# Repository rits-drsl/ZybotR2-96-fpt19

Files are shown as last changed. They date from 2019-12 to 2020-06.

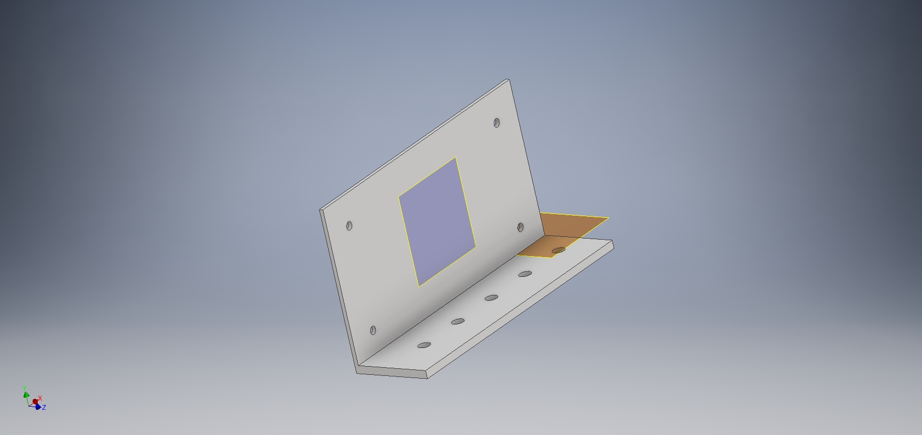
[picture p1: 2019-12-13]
assets/cad/avhzy_mounter/avhzy_mounter.jpg

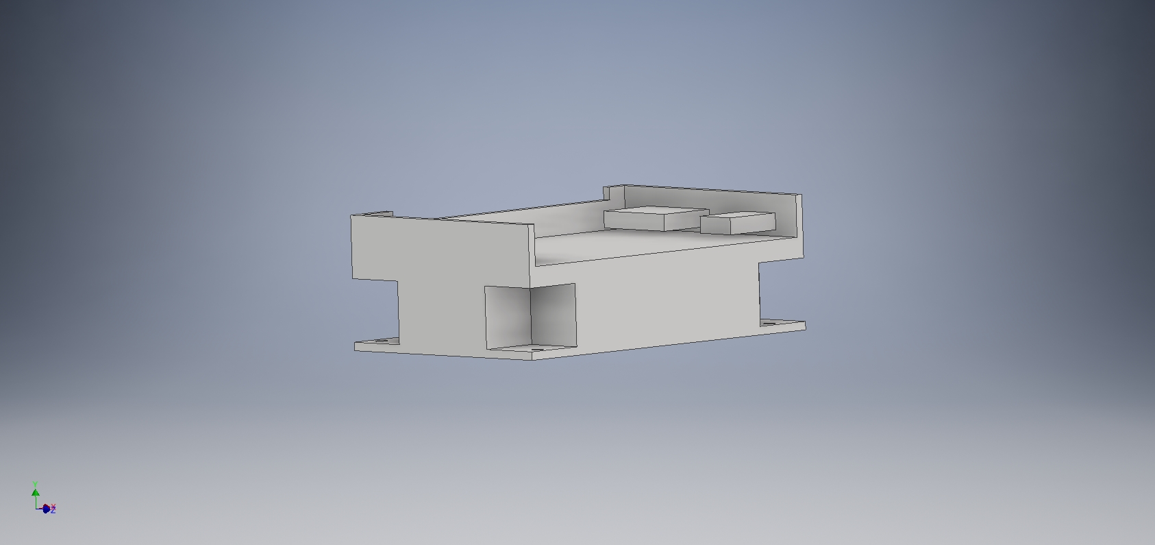
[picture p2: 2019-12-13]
assets/cad/ultra96_holder/ultra96_holder.jpg

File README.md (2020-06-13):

# ZybotR2-96-fpt19
An UGV-system using SoC-FPGA developed for FPGA design competition held on ICFPT2019.

**Our team won first place! :tada: :tada: :tada:**
<p align="center">
    ZybotR2-96
</p>

## Features
- **Localization** and **Motion Planning** are implemented in the UGV-system
    - In the **Localization** process, observations such as **Wheel Odometry** are fusioned by **Particle Filter**
    - In the **Motion Planning** process, **Informed-RRT\***, **Pure Pursuit**, and **PID control** are used
debug

- Efficient data flow that image data captured by image sensor are processed by FPGA before transferring to DRAM
- Peripheral devices (e.g. DC motor) can be handled transparently from Zynq PS by a system that synchronize registers between multiple FPGAs with UART
<p align="center">
    architecture
</p>

- The UGV-system is divided into **five layers**, and it is descending order of abstraction
<p align="center">
    system_layer
</p>

## Main Parts of The Vehicle
- [Avnet Ultra96 V1](https://www.xilinx.com/products/boards-and-kits/1-vad4rl.html)
- [Digilent Cmod A7-35T](https://reference.digilentinc.com/reference/programmable-logic/cmod-a7/start/)
- [96Boards MIPI Adapter Mezzanine](https://www.96boards.org/product/mipiadapter/)
- [Pcam5C](https://store.digilentinc.com/pcam-5c-5-mp-fixed-focus-color-camera-module/)
- [Web Camera (Buffalo BSW20KM11BK)](https://www.buffalo.jp/product/detail/bsw20km11bk.html)
- [Stereo Camera (Optor)](https://www.seeedstudio.com/Optor-Cam2pc-Visual-Inertial-SLAM-p-307.html)
- [Anker PowerCore+ 26800 PD](https://www.anker.com/products/variant/powercore--26800-pd-with-30w-power-delivery-charger/B1375112)
- [DC Motor/Gearbox (1:53 Gear Ratio)](https://store.digilentinc.com/dc-motor-gearbox-1-53-gear-ratio-custom-6v-motor-designed-for-digilent-robot-kits/)

## Repository Structure
A part of this repository structure is shown below:

``` sh
ZybotR2-96-fpt19
├── assets
│   ├── cad
│   ├── script
│   └── tools
├── cmod-a7
│   └── vivado
│       ├── prj
│       └── src
└── ultra96
    ├── BOOT_FS
    ├── ROOT_FS
    │   ├── app
    │   │   ├── fad
    │   │   └── other
    │   ├── driver
    │   │   ├── cp210x
    │   │   ├── usbserial
    │   │   └── v4l2
    │   ├── dts
    │   ├── firmware
    │   ├── lib
    │   │   ├── control
    │   │   ├── improc
    │   │   ├── optor
    │   │   ├── planner
    │   │   └── zynqpl
    │   └── package
    └── vivado
        ├── ip
        ├── prj
        └── src
```

- `assets/`
    - 3DCAD data for the vehicle parts, scripts which install libraries such as OpenCV, and tools are stored
- `cmod/vivado/`
    - RTL files and scripts which create project are stored
    - A Registers synchronization module, a motor controller, and an OLED controller are implemented
- `ultra96/BOOT_FS/`
    - Binary files for booting Linux on Ultra96 are stored
    - These files are prepared with reference to [ikwzm/ZynqMP-FPGA-Linux](https://github.com/ikwzm/ZynqMP-FPGA-Linux)
- `ultra96/ROOT_FS/app/`
    - An application of FAD(FPGA Autonomous Driving), test applications of devices, and so on are stored
- `ultra96/ROOT_FS/lib/`
    - Shared libraries are stored
    - `planner` is based on [kyk0910/sampling-based-planners](https://github.com/kyk0910/sampling-based-planners)
    - `optor` is prepared with reference to [optor-vis/optor_vi-stereo-v1](https://github.com/optor-vis/optor_vi-stereo-v1)
- `ultra96/ROOT_FS/driver/`
    - Device drivers are stored
    - `v4l2` which is Linux V4L2 driver which deals with the Xilinx VDMA IP is prepared with reference to [fixstars/ultra96_design](https://github.com/fixstars/ultra96_design)
- `ultra96/ROOT_FS/dts/`
    - DTS(Device Tree Source) files are stored
    - We reflect some of device information to kernel using **Device Tree Overlay** which is feature of Linux kernel
- `ultra96/ROOT_FS/firmware/`
    - A bitstream file and firmware of wireless LAN modules are stored
    - A bitstream file is loaded with **FPGA Region** which is feature of Linux kernel
- `ultra96/ROOT_FS/package/`
    - Debian packages of **linux-headers** and **linux-image** are stored
    - There are also prepared with reference to [ikwzm/ZynqMP-FPGA-Linux](https://github.com/ikwzm/ZynqMP-FPGA-Linux)
- `ultra96/vivado/`
    - RTL files, HLS sources, IPs made by Digilent and scripts which create project are stored
    - `preimproc` module is based on [kyk0910/HLS-canny-edge-detection](https://github.com/kyk0910/HLS-canny-edge-detection)

## Future Work
- Offload computation heavy processes such as Informed-RRT*, Particle Filter, path tracking algorithms, and calculating Visual Odometry
- Implement more accurate image recognition algorithms

## Links
- [2019 International Conference on Field-Programmable Technology FPGA Design Competition](http://fpt19.tju.edu.cn/Contest/FPT2019_FPGA_Design_Competition.htm)

## Authors
- [Yuya Kudo](https://github.com/medalotte)
- [Atsushi Takada](https://github.com/atlchemt)
- [Yuta Ishida](https://github.com/yukkuriDo)
- Prof. Tomonori Izumi

## References
[Y. Kudo, A. Takada, Y. Ishida, and T. Izumi, "An SoC-FPGA-based Micro UGV with Localization and Motion Planning," in Proceedings of 2019 International Conference on Field-Programmable Technology (ICFPT), 2019, pp. 469-472.](https://ieeexplore.ieee.org/document/8977887)

## License
MIT

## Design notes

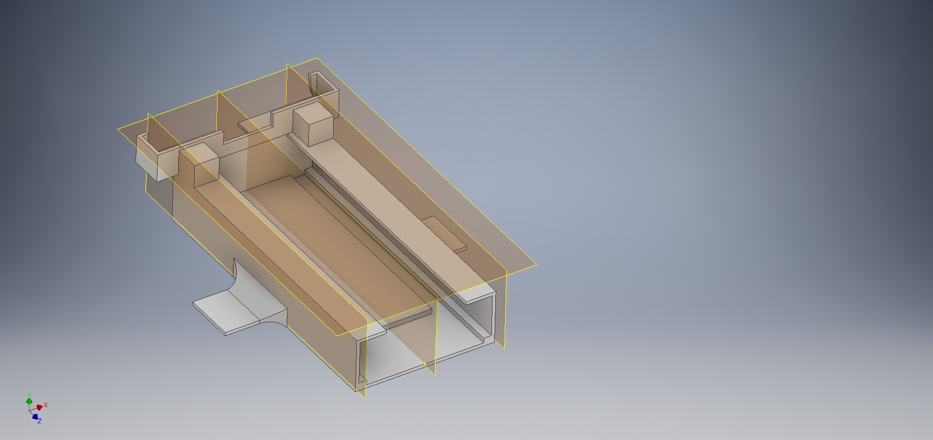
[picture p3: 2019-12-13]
assets/cad/battery_case/battery_case.jpg

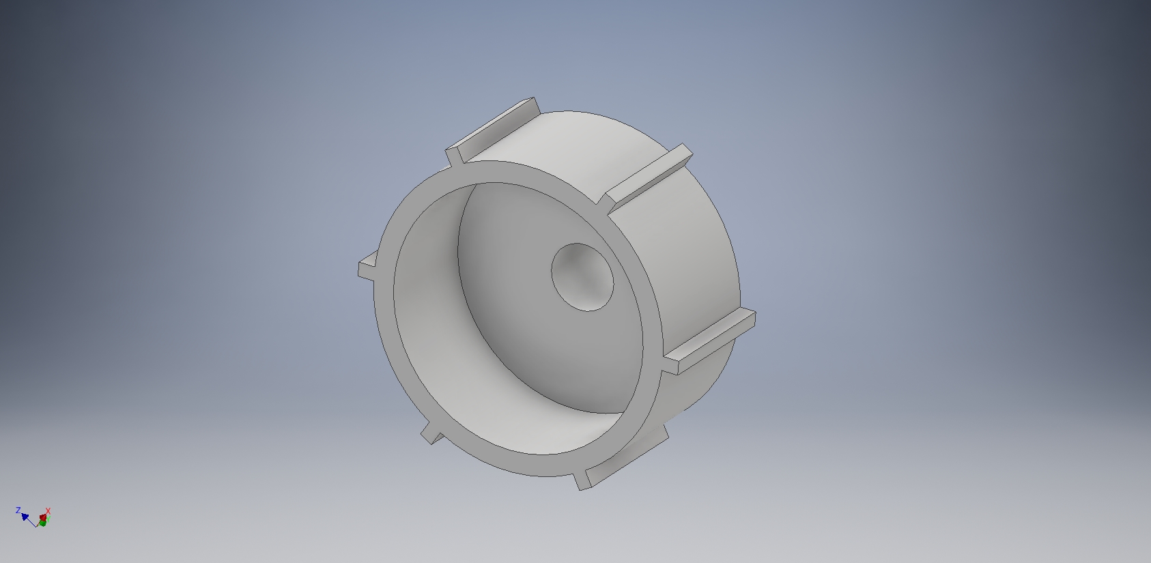
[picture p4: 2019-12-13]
assets/cad/camera_cap_holder/camera_cap_holder.jpg

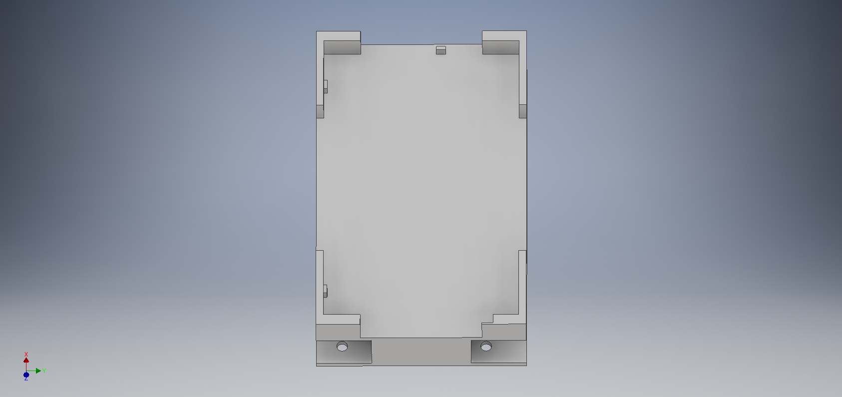
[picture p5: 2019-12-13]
assets/cad/cmod_a7_holder/cmod_a7_holder.jpg

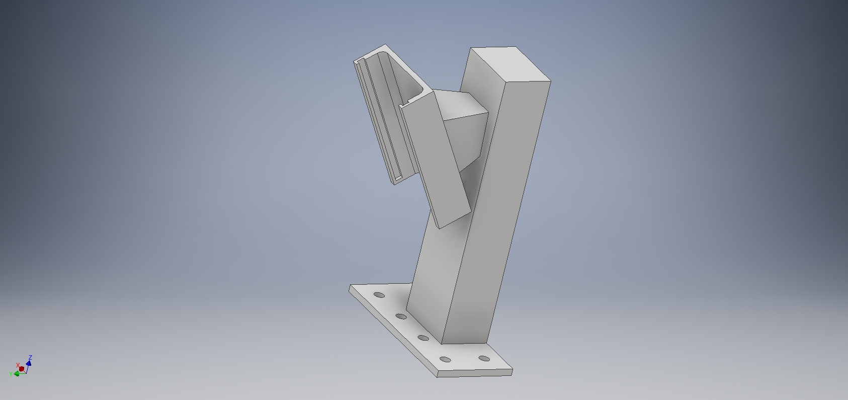
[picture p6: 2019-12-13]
assets/cad/Pcam5C/Pcam5C_mounter.jpg

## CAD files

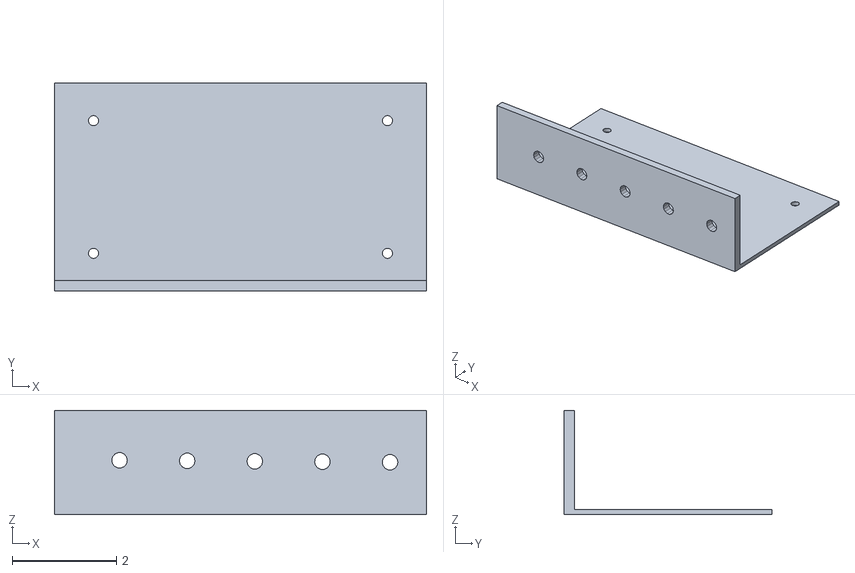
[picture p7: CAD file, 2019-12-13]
assets/cad/avhzy_mounter/avhzy_mounter.stl
7.15 x 4.00 x 2.00

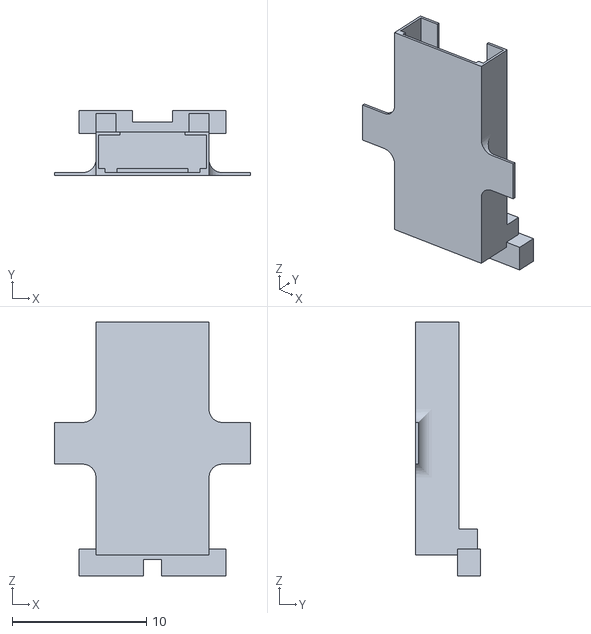
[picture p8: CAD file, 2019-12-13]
assets/cad/battery_case/battery_case.stl
14.6 x 4.82 x 19.0

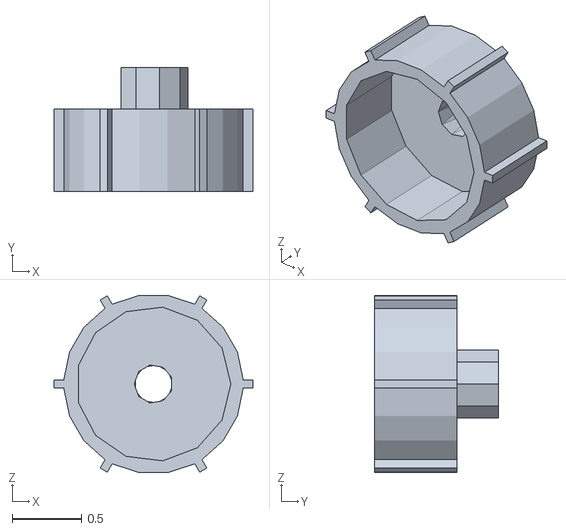
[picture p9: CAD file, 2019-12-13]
assets/cad/camera_cap_holder/camera_cap_holder.stl
1.44 x 0.9 x 1.28

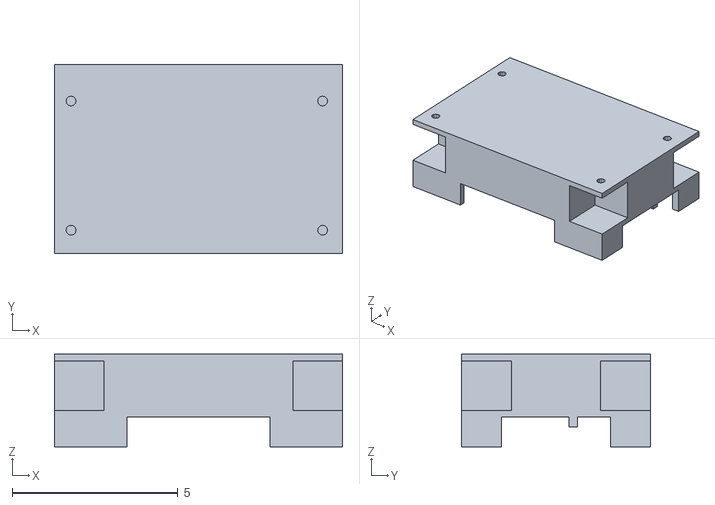
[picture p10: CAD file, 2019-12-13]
assets/cad/cmod_a7_holder/cmod_a7_holder.stl
8.70 x 5.70 x 2.80

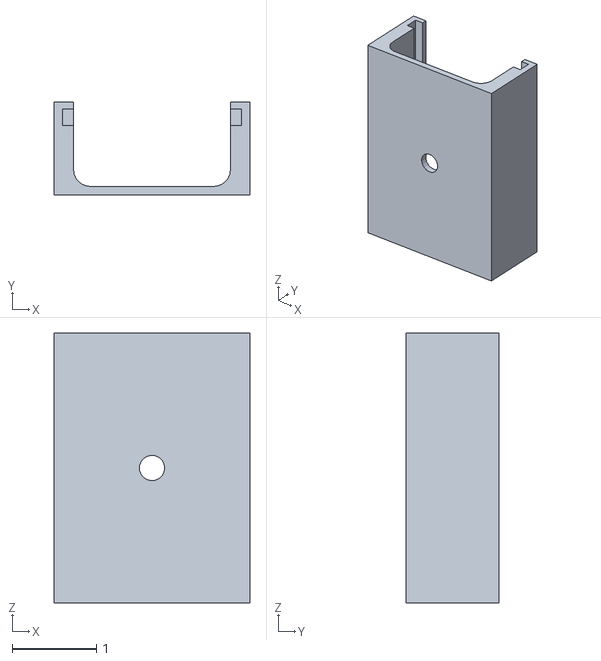
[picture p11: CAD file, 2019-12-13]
assets/cad/HB5_holder/HB5_holder.stl
2.32 x 1.10 x 3.20

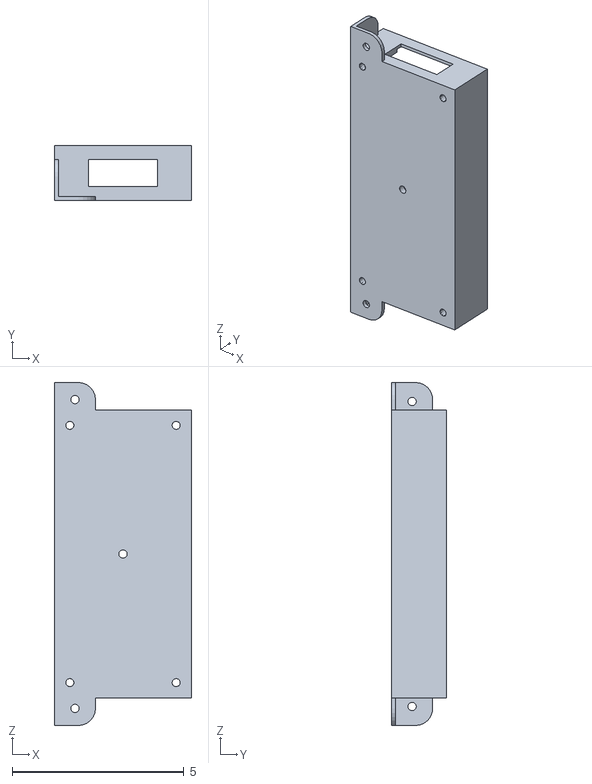
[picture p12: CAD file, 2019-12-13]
assets/cad/OLED_holder/OLED_holder.stl
4.00 x 1.60 x 10.0

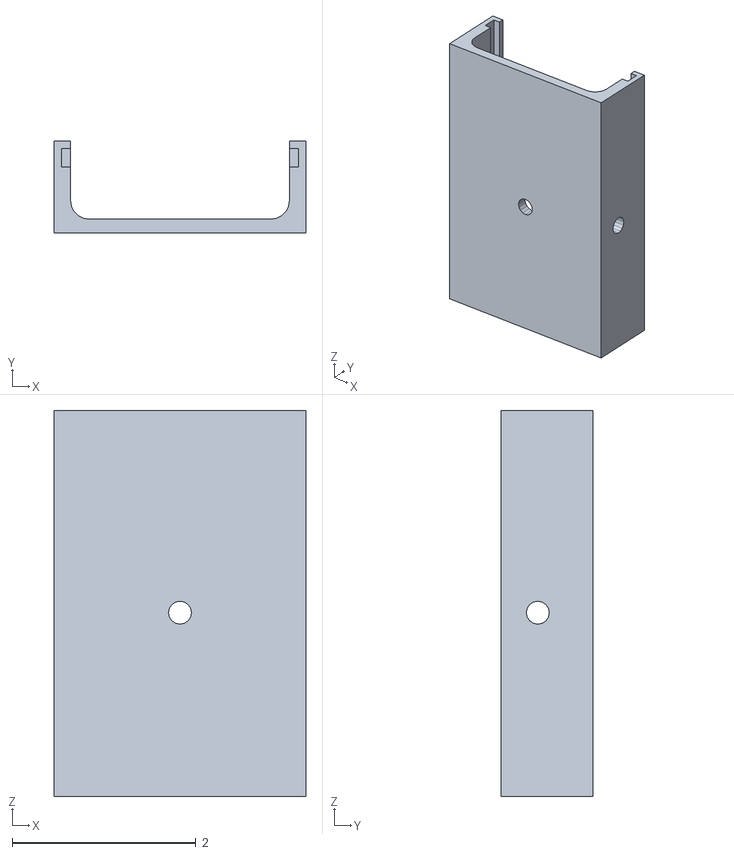
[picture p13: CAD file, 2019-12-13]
assets/cad/Pcam5C/Pcam5C_holder.stl
2.74 x 1.00 x 4.20

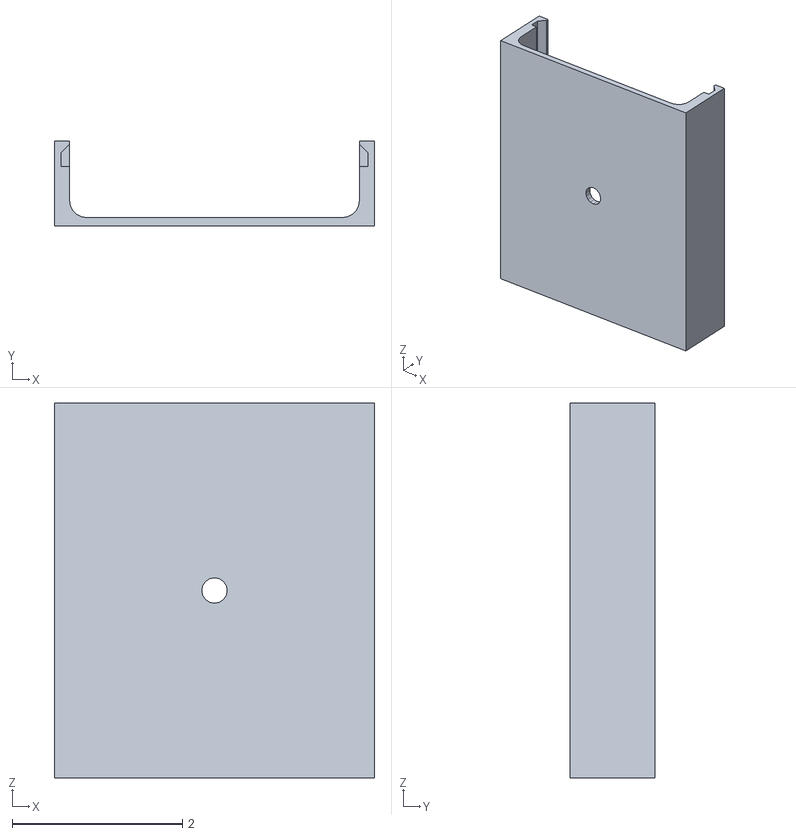
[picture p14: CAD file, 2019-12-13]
assets/cad/protection_circuit_holder/protection_circuit_holder.stl
3.76 x 1.00 x 4.40

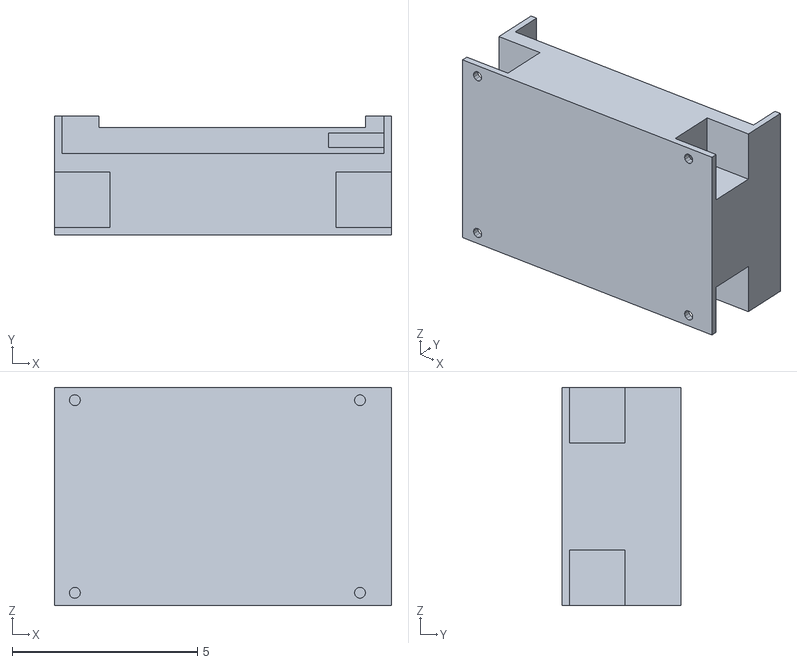
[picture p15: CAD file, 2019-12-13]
assets/cad/ultra96_holder/ultra96_holder.stl
9.10 x 3.20 x 5.90

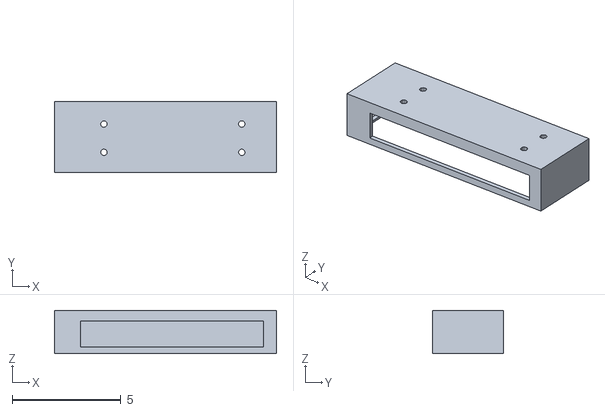
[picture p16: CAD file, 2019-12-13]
assets/cad/usb_hub_holder/usb_hub_holder.stl
10.2 x 3.25 x 2.00

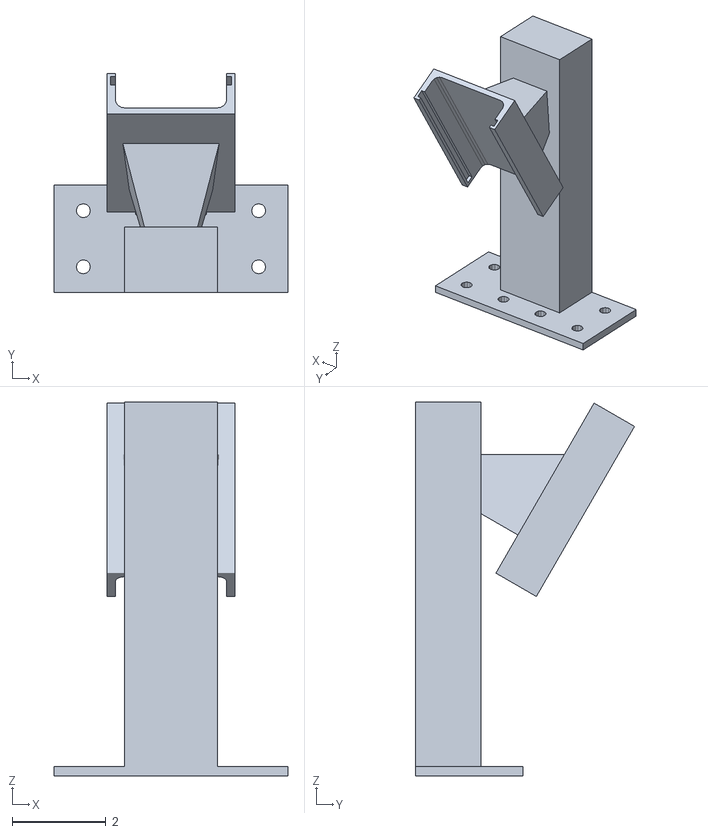
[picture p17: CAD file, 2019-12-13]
assets/cad/Pcam5C/Pcam5C_mounter.stl
5.00 x 4.69 x 8.00

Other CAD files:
assets/cad/HB5_holder/HB5_holder.ipt
assets/cad/OLED_holder/OLED_holder.ipt
assets/cad/Pcam5C/Pcam5C_holder.ipt
assets/cad/Pcam5C/Pcam5C_mounter.ipt
assets/cad/avhzy_mounter/avhzy_mounter.ipt
assets/cad/battery_case/battery_case.ipt
assets/cad/camera_cap_holder/camera_cap_holder.ipt
assets/cad/cmod_a7_holder/cmod_a7_holder.ipt
assets/cad/protection_circuit_holder/protection_circuit_holder.ipt
assets/cad/ultra96_holder/ultra96_holder.ipt
assets/cad/usb_hub_holder/usb_hub_holder.ipt

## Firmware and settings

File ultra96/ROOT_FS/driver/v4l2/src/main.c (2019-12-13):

#include <linux/kernel.h>
#include <linux/module.h>
#include <linux/types.h>
#include <linux/of_platform.h>
#include <linux/dma-mapping.h>
#include <linux/interrupt.h>
#include <linux/poll.h>
#include <linux/videodev2.h>
#include "zynq_v4l2.h"

MODULE_DESCRIPTION("ZYNQ v4l2 device driver");
MODULE_AUTHOR("takashi.osawa");
MODULE_LICENSE("GPL");

int vdma_h_res = 1280;
int vdma_v_res = 720;
module_param(vdma_h_res, int, S_IRUGO);
module_param(vdma_v_res, int, S_IRUGO);
MODULE_PARM_DESC(vdma_h_res, "v4l2 buffer width");
MODULE_PARM_DESC(vdma_v_res, "v4l2 buffer height");

int zynq_v4l2_find_oldest_slot(uint32_t slot_bits, int latest)
{
    uint32_t bits = slot_bits;

    bits &= ~(((1 << latest) << 1) - 1);
    if (bits ) {
        return __builtin_ctz(bits);
    } else if (slot_bits) {
        return __builtin_ctz(slot_bits);
    } else {
        return -1;
    }
}

static int zynq_v4l2_open(struct inode *inode, struct file *filp)
{
    struct zynq_v4l2_sys_data *sp;
    struct zynq_v4l2_dev_data *dp;
    int minor;

    PRINTK(KERN_INFO "%s\n", __FUNCTION__);

    sp = container_of(inode->i_cdev, struct zynq_v4l2_sys_data, cdev);
    if (sp == NULL) {
        printk(KERN_ERR "container_of failed\n");
        return -EFAULT;
    }
    minor = iminor(inode);
    dp = &sp->dev[minor];
    filp->private_data = dp;

    return 0;
}

static int zynq_v4l2_close(struct inode *inode, struct file *filp)
{
    struct zynq_v4l2_dev_data *dp = filp->private_data;

    PRINTK(KERN_INFO "%s\n", __FUNCTION__);

    zynq_v4l2_vdma_intr_disable(dp);
    spin_lock_irq(&dp->lock);
    dp->ctrl.queue_bits = 0;
    dp->ctrl.active_bits = 0;
    spin_unlock_irq(&dp->lock);
    while (dp->ctrl.work_queue_active) {
        schedule();
    }
    if (dp->mem.mmap) {
        #ifdef USE_VMALLOC
        vfree(dp->mem.mmap);
        #else /* !USE_VMALLOC */
        dma_free_coherent(dp->dma_dev, ALIGN(dp->frame.size, PAGE_SIZE) * dp->frame.user_count, dp->mem.mmap, dp->mem.phys_mmap);
        #endif /* !USE_VMALLOC */
        dp->mem.mmap = NULL;
    }

    return 0;
}

static ssize_t zynq_v4l2_read(struct file *filp, char __user *buf, size_t count, loff_t *f_pos)
{
    struct zynq_v4l2_dev_data *dp = filp->private_data;
    int wb;

    if (count > vdma_h_res * vdma_v_res * 3) {
        return -EINVAL;
    }

    wb = XAxiVdma_CurrFrameStore(dp->vdma.inst, XAXIVDMA_WRITE);
    wb = (wb + dp->vdma.inst->MaxNumFrames - 1) % dp->vdma.inst->MaxNumFrames;
    printk(KERN_INFO "%s wb = %d\n", __FUNCTION__, wb);
    if (raw_copy_to_user(buf, dp->vdma.virt_wb + dp->frame.size * wb, count) != 0) {
        return -EFAULT;
    }

    return count;
}

static ssize_t zynq_v4l2_write(struct file *filp, const char __user *buf, size_t count, loff_t *f_pos)
{
    PRINTK(KERN_INFO "%s\n", __FUNCTION__);

    return 0;
}

static unsigned int zynq_v4l2_poll(struct file *filp, struct poll_table_struct *waitp)
{
    struct zynq_v4l2_dev_data *dp = filp->private_data;
    int slot, rc;

    PRINTK(KERN_INFO "%s\n", __FUNCTION__);

    spin_lock_irq(&dp->lock);
    slot = zynq_v4l2_find_oldest_slot(dp->ctrl.active_bits, dp->ctrl.latest_frame);
    spin_unlock_irq(&dp->lock);

    if (slot == -1) {
        poll_wait(filp, &dp->ctrl.waitq, waitp);
        spin_lock_irq(&dp->lock);
        if ((slot = zynq_v4l2_find_oldest_slot(dp->ctrl.active_bits, dp->ctrl.latest_frame)) == -1) {
            rc = 0;
        } else {
            rc = (POLLIN | POLLRDNORM);
        }
        spin_unlock_irq(&dp->lock);
    } else {
        rc = (POLLIN | POLLRDNORM);
    }
    PRINTK(KERN_INFO "  rc = %d, slot = %d\n", rc, slot);

    return rc;
}

static int zynq_v4l2_vma_fault(struct vm_fault *vmf)
{
    struct page *page;
    unsigned long offset = vmf->pgoff << PAGE_SHIFT;
    struct zynq_v4l2_dev_data *dp = vmf->vma->vm_private_data;

    if (offset > dp->frame.size * dp->frame.user_count) {
        return VM_FAULT_SIGBUS;
    }

    #ifdef USE_VMALLOC
    page = vmalloc_to_page((void *)((unsigned long)dp->mem.mmap + offset));
    #else /* !USE_VMALLOC */
    page = phys_to_page(dp->mem.phys_mmap + offset);
    #endif /* !USE_VMALLOC */
    get_page(page);
    vmf->page = page;

    return 0;
}

static struct vm_operations_struct zynq_v4l2_vm_ops = {
                                                       .fault = zynq_v4l2_vma_fault,
};

static int zynq_v4l2_mmap(struct file *filp, struct vm_area_struct *vma)
{
    struct zynq_v4l2_dev_data *dp = filp->private_data;

    PRINTK(KERN_INFO "%s\n", __FUNCTION__);

    if ((vma->vm_pgoff + vma_pages(vma)) > ((ALIGN(dp->frame.size, PAGE_SIZE) * dp->frame.user_count) >> PAGE_SHIFT)) {
        return -EINVAL;
    }

    vma->vm_private_data = dp;
    vma->vm_ops = &zynq_v4l2_vm_ops;

    return 0;
}

static struct file_operations zynq_v4l2_fops = {
                                                .open           = zynq_v4l2_open,
                                                .release        = zynq_v4l2_close,
                                                .read           = zynq_v4l2_read,
                                                .write          = zynq_v4l2_write,
                                                .poll           = zynq_v4l2_poll,
                                                .unlocked_ioctl = zynq_v4l2_ioctl,
                                                .compat_ioctl   = zynq_v4l2_ioctl,
                                                .mmap           = zynq_v4l2_mmap,
};

static int zynq_v4l2_create_cdev(struct device *parent, struct zynq_v4l2_sys_data *sp)
{
    int ret;
    dev_t dev;
    int minor;

    PRINTK(KERN_INFO "%s\n", __FUNCTION__);

    ret = alloc_chrdev_region(&dev, MINOR_BASE, MINOR_NUM, DRIVER_NAME);
    if (ret != 0) {
        printk(KERN_ERR "alloc_chrdev_region = %d\n", ret);
        return -1;
    }

    sp->class = class_create(THIS_MODULE, DRIVER_NAME);
    if (IS_ERR(sp->class)) {
        printk(KERN_ERR "class_create\n");
        goto error;
    }

    cdev_init(&sp->cdev, &zynq_v4l2_fops);
    sp->cdev.owner = THIS_MODULE;
    sp->major = MAJOR(dev);

    ret = cdev_add(&sp->cdev, dev, MINOR_NUM);
    if (ret != 0) {
        printk(KERN_ERR "cdev_add = %d\n", ret);
        goto error;
    }
    sp->cdev_inited = true;

    for (minor = 0; minor < MINOR_NUM; minor++) {
        struct zynq_v4l2_dev_data *dp = &sp->dev[minor];

        device_create(sp->class, parent, MKDEV(sp->major, minor), dp, "pcam%d", minor);
        dp->dma_dev = parent;
    }

    return 0;

 error:
    for (minor = 0; minor < MINOR_NUM; minor++) {
        if (sp->class) {
            device_destroy(sp->class, MKDEV(sp->major, minor));
        }
    }
    if (sp->cdev_inited) {
        cdev_del(&sp->cdev);
        sp->cdev_inited = false;
    }
    if (sp->class) {
        class_destroy(sp->class);
        sp->class = NULL;
    }
    unregister_chrdev_region(dev, MINOR_NUM);

    return -1;
}

static void zynq_v4l2_delete_cdev(struct zynq_v4l2_sys_data *sp)
{
    int minor;
    dev_t dev = MKDEV(sp->major, MINOR_BASE);

    PRINTK(KERN_INFO "%s\n", __FUNCTION__);

    for (minor = MINOR_BASE; minor < MINOR_BASE + MINOR_NUM; minor++) {
        device_destroy(sp->class, MKDEV(sp->major, minor));
    }
    if (sp->cdev_inited) {
        cdev_del(&sp->cdev);
    }
    class_destroy(sp->class);
    unregister_chrdev_region(dev, MINOR_NUM);
}

static int zynq_v4l2_hw_init(struct device *dev, struct zynq_v4l2_sys_data *sp)
{
    int minor, rc;

    PRINTK(KERN_INFO "%s\n", __FUNCTION__);

    if (zynq_v4l2_vdma_init(dev, sp)) {
        return -ENODEV;
    }

    /* if (zynq_v4l2_demosaic_init()) { */
    /*      rc = -ENODEV; */
    /*      goto error; */
    /* } */

    if (zynq_v4l2_mipicsi_init()) {
        rc = -ENODEV;
        goto error;
    }

    return 0;

 error:
    for (minor = 0; minor < MINOR_NUM; minor++) {
        struct zynq_v4l2_dev_data *dp = &sp->dev[minor];

        free_irq(dp->vdma.irq_num, dp);
        dma_free_coherent(dp->dma_dev, dp->vdma.alloc_size_wb, dp->vdma.virt_wb, dp->vdma.phys_wb);
        iounmap(dp->vdma.reg);
    }

    return rc;
}

static void zynq_v4l2_free_data_all(struct zynq_v4l2_sys_data *sp)
{
    int minor;

    for (minor = 0; minor < MINOR_NUM; minor++) {
        struct zynq_v4l2_dev_data *dp = &sp->dev[minor];

        if (dp->vdma.irq_num) {
            free_irq(dp->vdma.irq_num, dp);
        }
        if (dp->vdma.virt_wb) {
            dma_free_coherent(dp->dma_dev, dp->vdma.alloc_size_wb, dp->vdma.virt_wb, dp->vdma.phys_wb);
        }
        if (dp->vdma.reg) {
            iounmap(dp->vdma.reg);
        }
        if (dp->mem.mmap) {
            #ifdef USE_VMALLOC
            vfree(dp->mem.mmap);
            #else /* !USE_VMALLOC */
            dma_free_coherent(dp->dma_dev, ALIGN(dp->frame.size, PAGE_SIZE) * dp->frame.user_count, dp->mem.mmap, dp->mem.phys_mmap);
            #endif /* !USE_VMALLOC */
        }
    }
    if (sp->cdev_inited) {
        zynq_v4l2_delete_cdev(sp);
    }
    if (sp->wq) {
        flush_workqueue(sp->wq);
        destroy_workqueue(sp->wq);
    }
    kfree(sp);
}

static int zynq_v4l2_probe(struct platform_device *pdev)
{
    int minor;
    struct device *dev = &pdev->dev;
    struct zynq_v4l2_sys_data *sp;

    dev_info(dev, "Device Tree Probing");
    printk(KERN_INFO "%s\n", __FUNCTION__);

    sp = (struct zynq_v4l2_sys_data *)kzalloc(sizeof(struct zynq_v4l2_sys_data), GFP_KERNEL);
    if (!sp) {
        dev_err(dev, "Could not allocate memory\n");
        return -ENOMEM;
    }

    if (zynq_v4l2_create_cdev(&pdev->dev, sp)) {
        dev_err(dev, "zynq_v4l2_create_cdev failed\n");
        zynq_v4l2_free_data_all(sp);
        dev_set_drvdata(dev, NULL);
        return -EBUSY;
    }

    if (zynq_v4l2_hw_init(&pdev->dev, sp)) {
        dev_err(dev, "hw_init failed\n");
        zynq_v4l2_free_data_all(sp);
        dev_set_drvdata(dev, NULL);
        return -ENODEV;
    }

    sp->wq = create_workqueue("zynq_v4l2_wq");
    if (!sp->wq) {
        dev_err(dev, "create_workqueue failed\n");
        zynq_v4l2_free_data_all(sp);
        dev_set_drvdata(dev, NULL);
        return -ENODEV;
    }

    for (minor = 0; minor < MINOR_NUM; minor++) {
        struct zynq_v4l2_dev_data *dp = &sp->dev[minor];

        spin_lock_init(&dp->lock);
        init_waitqueue_head(&dp->ctrl.waitq);
        dp->ctrl.latest_frame = dp->vdma.inst->MaxNumFrames - 1;
        dp->frame.user_count = MAX_USER_MEM;
        dp->sp = sp;
    }

    dev_set_drvdata(dev, sp);

    return 0;
}

static int zynq_v4l2_remove(struct platform_device *pdev)
{
    struct device *dev = &pdev->dev;
    struct zynq_v4l2_sys_data *sp = dev_get_drvdata(dev);

    printk(KERN_INFO "%s\n", __FUNCTION__);

    zynq_v4l2_free_data_all(sp);
    dev_set_drvdata(dev, NULL);

    return 0;
}

#ifdef CONFIG_OF
static struct of_device_id zynq_v4l2_of_match[] = {
                                                   { .compatible = "fixstars,zynq-v4l2-1.0", },
                                                   { /* end of table */ },
};
MODULE_DEVICE_TABLE(of, zynq_v4l2_of_match);
#else
#define zynq_v4l2_of_match
#endif

static struct platform_driver zynq_v4l2_driver = {
                                                  .driver = {
                                                             .name = DRIVER_NAME,
                                                             .owner = THIS_MODULE,
                                                             .of_match_table = zynq_v4l2_of_match,
                                                             },
                                                  .probe = zynq_v4l2_probe,
                                                  .remove = zynq_v4l2_remove,
};

static int zynq_v4l2_init(void)
{
    printk(KERN_INFO "%s\n", __FUNCTION__);

    return platform_driver_register(&zynq_v4l2_driver);
}

static void zynq_v4l2_exit(void)
{
    printk(KERN_INFO "%s\n", __FUNCTION__);
    platform_driver_unregister(&zynq_v4l2_driver);
}

module_init(zynq_v4l2_init);
module_exit(zynq_v4l2_exit);

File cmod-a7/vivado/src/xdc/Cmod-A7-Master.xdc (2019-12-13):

## This file is a general .xdc for the CmodA7 rev. B
## To use it in a project:
## - uncomment the lines corresponding to used pins
## - rename the used ports (in each line, after get_ports) according to the top level signal names in the project

## 12 MHz Clock Signal
set_property -dict { PACKAGE_PIN L17   IOSTANDARD LVCMOS33 } [get_ports { sysclk }]; #IO_L12P_T1_MRCC_14 Sch=gclk
create_clock -add -name sys_clk_pin -period 83.33 -waveform {0 41.66} [get_ports {sysclk}];

## LEDs
set_property -dict { PACKAGE_PIN A17   IOSTANDARD LVCMOS33 } [get_ports { led[0] }]; #IO_L12N_T1_MRCC_16 Sch=led[1]p
set_property -dict { PACKAGE_PIN C16   IOSTANDARD LVCMOS33 } [get_ports { led[1] }]; #IO_L13P_T2_MRCC_16 Sch=led[2]

## RGB LED
set_property -dict { PACKAGE_PIN B17   IOSTANDARD LVCMOS33 } [get_ports { led0_b }]; #IO_L14N_T2_SRCC_16 Sch=led0_b
set_property -dict { PACKAGE_PIN B16   IOSTANDARD LVCMOS33 } [get_ports { led0_g }]; #IO_L13N_T2_MRCC_16 Sch=led0_g
set_property -dict { PACKAGE_PIN C17   IOSTANDARD LVCMOS33 } [get_ports { led0_r }]; #IO_L14P_T2_SRCC_16 Sch=led0_r

## Buttons
set_property -dict { PACKAGE_PIN A18   IOSTANDARD LVCMOS33 } [get_ports { btn[0] }]; #IO_L19N_T3_VREF_16 Sch=btn[0]
set_property -dict { PACKAGE_PIN B18   IOSTANDARD LVCMOS33 } [get_ports { btn[1] }]; #IO_L19P_T3_16 Sch=btn[1]

## Pmod Header JA
set_property -dict { PACKAGE_PIN G17   IOSTANDARD LVCMOS33 } [get_ports { ja[0] }]; #IO_L5N_T0_D07_14 Sch=ja[1]
set_property -dict { PACKAGE_PIN G19   IOSTANDARD LVCMOS33 } [get_ports { ja[1] }]; #IO_L4N_T0_D05_14 Sch=ja[2]
set_property -dict { PACKAGE_PIN N18   IOSTANDARD LVCMOS33 } [get_ports { ja[2] }]; #IO_L9P_T1_DQS_14 Sch=ja[3]
set_property -dict { PACKAGE_PIN L18   IOSTANDARD LVCMOS33 } [get_ports { ja[3] }]; #IO_L8P_T1_D11_14 Sch=ja[4]
set_property -dict { PACKAGE_PIN H17   IOSTANDARD LVCMOS33 } [get_ports { ja[4] }]; #IO_L5P_T0_D06_14 Sch=ja[7]
set_property -dict { PACKAGE_PIN H19   IOSTANDARD LVCMOS33 } [get_ports { ja[5] }]; #IO_L4P_T0_D04_14 Sch=ja[8]
set_property -dict { PACKAGE_PIN J19   IOSTANDARD LVCMOS33 } [get_ports { ja[6] }]; #IO_L6N_T0_D08_VREF_14 Sch=ja[9]
set_property -dict { PACKAGE_PIN K18   IOSTANDARD LVCMOS33 } [get_ports { ja[7] }]; #IO_L8N_T1_D12_14 Sch=ja[10]

set_property PULLUP true [get_ports ja[0]]
set_property PULLUP true [get_ports ja[1]]
set_property PULLUP true [get_ports ja[2]]
set_property PULLUP true [get_ports ja[3]]
set_property PULLUP true [get_ports ja[4]]
set_property PULLUP true [get_ports ja[5]]
set_property PULLUP true [get_ports ja[6]]
set_property PULLUP true [get_ports ja[7]]

## Analog XADC Pins
## Only declare these if you want to use pins 15 and 16 as single ended analog inputs. pin 15 -> vaux4, pin16 -> vaux12
#set_property -dict { PACKAGE_PIN G2    IOSTANDARD LVCMOS33 } [get_ports { xa_n[0] }]; #IO_L1N_T0_AD4N_35 Sch=ain_n[15]
#set_property -dict { PACKAGE_PIN G3    IOSTANDARD LVCMOS33 } [get_ports { xa_p[0] }]; #IO_L1P_T0_AD4P_35 Sch=ain_p[15]
#set_property -dict { PACKAGE_PIN J2    IOSTANDARD LVCMOS33 } [get_ports { xa_n[1] }]; #IO_L2N_T0_AD12N_35 Sch=ain_n[16]
#set_property -dict { PACKAGE_PIN H2    IOSTANDARD LVCMOS33 } [get_ports { xa_p[1] }]; #IO_L2P_T0_AD12P_35 Sch=ain_p[16]
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

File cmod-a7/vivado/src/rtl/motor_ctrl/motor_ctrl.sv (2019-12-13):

/*
 MIT License

 Copyright (c) 2019 Yuya Kudo

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
 THE SOFTWARE IS PROVIDED "AS IS", WITHOUT WARRANTY OF ANY KIND, EXPRESS OR
 IMPLIED, INCLUDING BUT NOT LIMITED TO THE WARRANTIES OF MERCHANTABILITY,
 FITNESS FOR A PARTICULAR PURPOSE AND NONINFRINGEMENT. IN NO EVENT SHALL THE
 AUTHORS OR COPYRIGHT HOLDERS BE LIABLE FOR ANY CLAIM, DAMAGES OR OTHER
 LIABILITY, WHETHER IN AN ACTION OF CONTRACT, TORT OR OTHERWISE, ARISING FROM,
 OUT OF OR IN CONNECTION WITH THE SOFTWARE OR THE USE OR OTHER DEALINGS IN THE
 SOFTWARE.
 */

`include "../if/w_busif.sv"
`include "../if/r_busif.sv"

//-----------------------------------------------------------------------------
// module      : モータ制御モジュール
// description : 機能一覧
//               1. PWM波形生成
//               2. PID制御器によるフィードバック制御
//               3. ロータリーエンコーダのカウント
module motor_ctrl
  #(parameter
    CLK_FREQ                   = 100_000_000,
    READ_ROT_VELOCITY_INTERVAL = 100,
    READ_GAIN_INTERVAL         = 1000000,
    WRITE_ROT_CNT_INTERVAL     = 1000000,
    WRITE_ROT_CNT_OFFSET       = 0,
    ADDR_ROTATION_VELOCITY     = 8'h00,
    ADDR_PROPORTION_GAIN       = 8'h00,
    ADDR_INTEGRATION_GAIN      = 8'h00,
    ADDR_DERIVATIVE_GAIN       = 8'h00,
    ADDR_ROT_CNT               = 8'h00,
    localparam
    BAND_WIDTH                 = 32,
    ONE_ROTATION_PULSE         = 630,
    SAMPLING_RATE              = 100,
    PWM_PERIOD                 = 40,  // us
    PWM_PERIOD_CYCLE           = (CLK_FREQ / 100_000) * PWM_PERIOD)
   (w_busif.master                w_m,
    r_busif.master                r_m,
    output logic                  pwm,
    output logic                  dir,
    output logic [BAND_WIDTH-1:0] pulse_width,
    output logic [BAND_WIDTH-1:0] rot_cnt,
    output logic [31:0]           target_rot_v,
    input  logic                  sa,
    input  logic                  sb,
    input  logic                  clk,
    input  logic                  rstn);

   logic [BAND_WIDTH-1:0] pwm_pulse_width;
   logic [BAND_WIDTH-1:0] p_gain;
   logic [BAND_WIDTH-1:0] i_gain;
   logic [BAND_WIDTH-1:0] d_gain;

   write_param_ctrl #(.ADDR_ROT_CNT(ADDR_ROT_CNT),
                      .WRITE_ROT_CNT_INTERVAL(WRITE_ROT_CNT_INTERVAL),
                      .WRITE_ROT_CNT_OFFSET(WRITE_ROT_CNT_OFFSET))
   write_param_ctrl_inst(.w_m(w_m),
                         .rot_cnt(rot_cnt),
                         .clk(clk),
                         .rstn(rstn));

   read_param_ctrl #(.READ_ROT_VELOCITY_INTERVAL(READ_ROT_VELOCITY_INTERVAL),
                     .READ_GAIN_INTERVAL(READ_GAIN_INTERVAL),
                     .ADDR_ROTATION_VELOCITY(ADDR_ROTATION_VELOCITY),
                     .ADDR_PROPORTION_GAIN(ADDR_PROPORTION_GAIN),
                     .ADDR_INTEGRATION_GAIN(ADDR_INTEGRATION_GAIN),
                     .ADDR_DERIVATIVE_GAIN(ADDR_DERIVATIVE_GAIN))
   read_param_ctrl_inst(.r_m(r_m),
                        .rot_v(target_rot_v),
                        .p_gain(p_gain),
                        .i_gain(i_gain),
                        .d_gain(d_gain),
                        .clk(clk),
                        .rstn(rstn));

   pwm_generator #(.BAND_WIDTH(BAND_WIDTH),
                   .PWM_PERIOD_CYCLE(PWM_PERIOD_CYCLE))
   pwm_gen_inst(.width(pwm_pulse_width),
                .pwm(pwm),
                .clk(clk),
                .rstn(rstn));

   rot_encoder #(.BAND_WIDTH(BAND_WIDTH))
   rot_encoder_inst(.sa(sa),
                    .sb(sb),
                    .count(rot_cnt),
                    .clk(clk),
                    .rstn(rstn));

   pid_controller #(.BAND_WIDTH(BAND_WIDTH),
                    .CLK_FREQ(CLK_FREQ),
                    .ONE_ROTATION_PULSE(ONE_ROTATION_PULSE),
                    .SAMPLING_RATE(SAMPLING_RATE))
   pid_ctrl_inst(.target_rot_v(target_rot_v),
                 .p_gain(p_gain),
                 .i_gain(i_gain),
                 .d_gain(d_gain),
                 .rot_cnt(rot_cnt),
                 .pulse_width(pulse_width),
                 .clk(clk),
                 .rstn(rstn));

   assign dir             = pulse_width[31:31] ? 1'b1 : 1'b0;
   assign pwm_pulse_width = pulse_width[31:31] ? ~pulse_width : pulse_width;

endmodule

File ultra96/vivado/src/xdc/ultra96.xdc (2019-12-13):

# ----------------------------------------------------------------------------
#       __ __
#      / / \ \
#     / /   \ \
#    / /     \ \
#   / / AVNET \ \          www.ultra96.org
#
# ----------------------------------------------------------------------------
#
#  Created With Avnet Constraints Generator V0.8.0
#     Date: Sunday, March 18, 2018
#     Time: 1:00:11 AM
#
#  This design is the property of Avnet.  Publication of this
#  design is not authorized without written consent from Avnet.
#
#  Please direct any questions to:
#     Avnet Ultra96 Forums
#     http://ultra96.org
#
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
# ----------------------------------------------------------------------------
#
#  Notes:
# 				2018 Mar 18 -- Initial version
#
#     IO standard for Bank 26 Vcco supply is fixed at 1.8V
#     IO standard for Bank 65 Vcco supply is fixed at 1.2V
#
#     Net names are not allowed to contain hyphen characters '-' since this
#     is not a legal VHDL87 or Verilog character within an identifier.
#     HDL net names are adjusted to contain no hyphen characters '-' but
#     rather use underscore '_' characters.  Comment net name with the hyphen
#     characters will remain in place since these are intended to match the
#     schematic net names in order to better enable schematic search.
#
# ----------------------------------------------------------------------------


# ----------------------------------------------------------------------------
# Bluetooth
# ----------------------------------------------------------------------------
# Bank 26
set_property PACKAGE_PIN C8   [get_ports {BT_AUD_CLK              }];  # "C8.BT_AUD_CLK"
set_property PACKAGE_PIN A8   [get_ports {BT_AUD_FSYNC            }];  # "A8.BT_AUD_FSYNC"
set_property PACKAGE_PIN A9   [get_ports {BT_AUD_IN               }];  # "A9.BT_AUD_IN"
set_property PACKAGE_PIN B9   [get_ports {BT_AUD_OUT              }];  # "B9.BT_AUD_OUT"
set_property PACKAGE_PIN B5   [get_ports {BT_HCI_CTS              }];  # "B5.BT_HCI_CTS"
set_property PACKAGE_PIN B7   [get_ports {BT_HCI_RTS              }];  # "B7.BT_HCI_RTS"

# ----------------------------------------------------------------------------
# High-speed expansion connector
# ----------------------------------------------------------------------------
# Bank 65
set_property PACKAGE_PIN P1   [get_ports {CSI0_C_N                }];  # "P1.CSI0_C_N"
set_property PACKAGE_PIN N2   [get_ports {CSI0_C_P                }];  # "N2.CSI0_C_P"
set_property PACKAGE_PIN N4   [get_ports {CSI0_D0_N               }];  # "N4.CSI0_D0_N"
set_property PACKAGE_PIN N5   [get_ports {CSI0_D0_P               }];  # "N5.CSI0_D0_P"
set_property PACKAGE_PIN M1   [get_ports {CSI0_D1_N               }];  # "M1.CSI0_D1_N"
set_property PACKAGE_PIN M2   [get_ports {CSI0_D1_P               }];  # "M2.CSI0_D1_P"
set_property PACKAGE_PIN M4   [get_ports {CSI0_D2_N               }];  # "M4.CSI0_D2_N"
set_property PACKAGE_PIN M5   [get_ports {CSI0_D2_P               }];  # "M5.CSI0_D2_P"
set_property PACKAGE_PIN L1   [get_ports {CSI0_D3_N               }];  # "L1.CSI0_D3_N"
set_property PACKAGE_PIN L2   [get_ports {CSI0_D3_P               }];  # "L2.CSI0_D3_P"
set_property PACKAGE_PIN T2   [get_ports {CSI1_C_N                }];  # "T2.CSI1_C_N"
set_property PACKAGE_PIN T3   [get_ports {CSI1_C_P                }];  # "T3.CSI1_C_P"
set_property PACKAGE_PIN R3   [get_ports {CSI1_D0_N               }];  # "R3.CSI1_D0_N"
set_property PACKAGE_PIN P3   [get_ports {CSI1_D0_P               }];  # "P3.CSI1_D0_P"
set_property PACKAGE_PIN U1   [get_ports {CSI1_D1_N               }];  # "U1.CSI1_D1_N"
set_property PACKAGE_PIN U2   [get_ports {CSI1_D1_P               }];  # "U2.CSI1_D1_P"
set_property PACKAGE_PIN H5   [get_ports {DSI_CLK_N               }];  # "H5.DSI_CLK_N"
set_property PACKAGE_PIN J5   [get_ports {DSI_CLK_P               }];  # "J5.DSI_CLK_P"
set_property PACKAGE_PIN F1   [get_ports {DSI_D0_N                }];  # "F1.DSI_D0_N"
set_property PACKAGE_PIN G1   [get_ports {DSI_D0_P                }];  # "G1.DSI_D0_P"
set_property PACKAGE_PIN E3   [get_ports {DSI_D1_N                }];  # "E3.DSI_D1_N"
set_property PACKAGE_PIN E4   [get_ports {DSI_D1_P                }];  # "E4.DSI_D1_P"
set_property PACKAGE_PIN D1   [get_ports {DSI_D2_N                }];  # "D1.DSI_D2_N"
set_property PACKAGE_PIN E1   [get_ports {DSI_D2_P                }];  # "E1.DSI_D2_P"
set_property PACKAGE_PIN C3   [get_ports {DSI_D3_N                }];  # "C3.DSI_D3_N"
set_property PACKAGE_PIN D3   [get_ports {DSI_D3_P                }];  # "D3.DSI_D3_P"
set_property PACKAGE_PIN C2   [get_ports {HSIC_DATA               }];  # "C2.HSIC_DATA"
# Bank 66
set_property PACKAGE_PIN A2   [get_ports {HSIC_STR                }];  # "A2.HSIC_STR"
# Bank 26
set_property PACKAGE_PIN E8   [get_ports {CSI0_MCLK               }];  # "E8.CSI0_MCLK"
set_property PACKAGE_PIN D8   [get_ports {CSI1_MCLK               }];  # "D8.CSI1_MCLK"
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

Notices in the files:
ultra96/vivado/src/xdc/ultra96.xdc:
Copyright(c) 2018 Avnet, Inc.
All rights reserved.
